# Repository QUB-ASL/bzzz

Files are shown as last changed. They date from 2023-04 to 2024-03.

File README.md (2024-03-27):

<p align="center">
bzzz-logo
</p>

<p align="center">
<em>Programmable quadcopter with ESP32 and RaspberryPi</em>
</p>

## Project Description

The autonomous systems lab at the school of EEECS of Queens University Belfast (QUB) has designed and built a quadcopter with a stabilising attitude control system and (as of v0.2.0) altitude hold. This is part of an ongoing research project whose objective is the development of control methodologies that will enable quadcopters to fly in extreme weather conditions. Currently, the quadcopter can be operated using a radio controller (RC).

## Getting started

- [Safety first](docs/SAFETY.md): read the safety guidelines
- [Contributing to this project](CONTRIBUTING.md)
- [Setting up software from scratch](docs/SETUP.md)
- [PCB design](design/README.md)
- [ESP32 documentation](include/README.md), [headers](./include) and [sources](./src)
- [Raspberry Pi code](raspberry/README.md)
- [Create a Discord bot](raspberry/DiscordBot/README.md)
- [Changelog](CHANGELOG.md)

## Design

The structure of the quadcopter is shown below

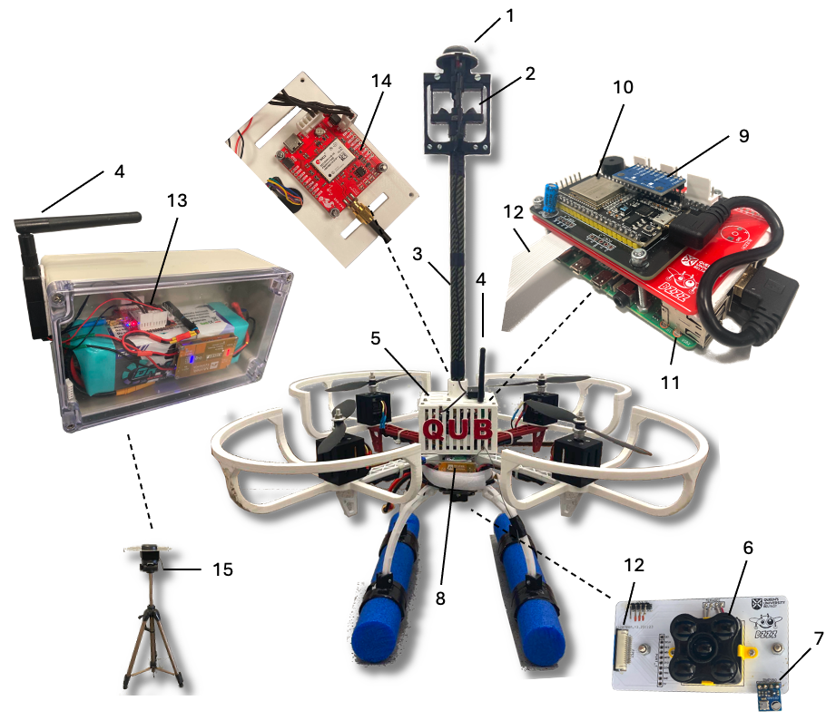
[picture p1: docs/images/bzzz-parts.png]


The parts shown in the figure are: 1. GNSS L1/L2 antenna, 2. 3D anemometer, 3. Carbon fibre pole, 4. Telemetry radio pair, 5. Box with electronics (Raspberry Pi, ESP32, IMU, GNSS module, radio receiver module), 6. Time-of-flight altimeter, 7. Barometer, 8. LiPo battery and UBEC, 9. IMU, 10. ESP32 microcontroller (attitude control system), 11. Raspberry Pi, 12. Interface between Raspberry Pi and sensors board, 13. Base station GNSS module, 14. GNSS module on the vehicle (inside the box), 15. Base GPS station.

A high-level schematic of the quadcopter with all its basic modules is shown below:

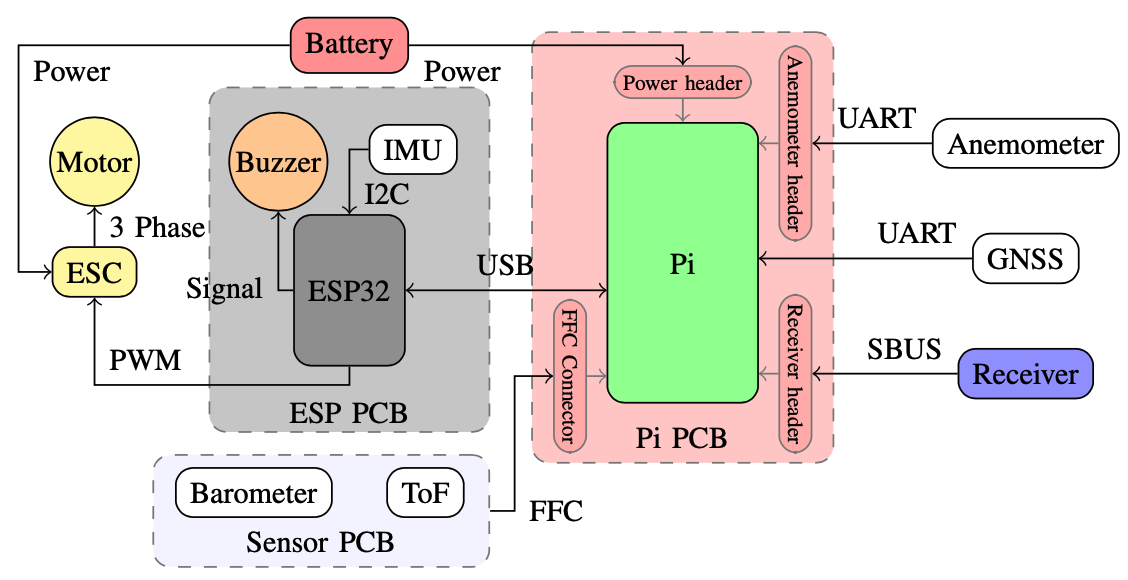
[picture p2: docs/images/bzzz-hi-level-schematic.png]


An ESP32 microcontroller is connected to an MPU9250 9-axis IMU and runs the attitude controller. 
A Raspberry Pi 4B computer is connected to a number of sensors (e.g., time-of-flight altimeter,
GPS module, and anemometer) and can run high-level tasks such as 
altitude and position control.
An RC receiver is connected to the Raspberry Pi and provides the commands of the operator.
The Raspberry Pi and the ESP32 microcontroller are connected with a USB and this allows
a bidirectional communication: the Raspberry sends tilt and throttle references to the 
ESP32 which in turn provides IMU measurements to the Raspberry Pi. 

## How to Fly 
*This is the current set up for how to fly the quadcopter*

- Make sure the quadcopter is in a safe place to fly
- Power on the battery
- Turn on the remote and wait to connect
- Arm the quadcopter by switch B
- Fly safely
- Switch D kills the quadcopter

## Videos 

<p>Testing altitude hold of bzzz:</p>

Watch the video (https://youtu.be/AMWUkB0SQi4)

<p>First flight of bzzz:</p>

Watch the video (https://youtu.be/eGNW_-LX130)

<p>Preliminary tests in the lab:</p>

Watch the video (https://youtu.be/7mFDusj9uvs)

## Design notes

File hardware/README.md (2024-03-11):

## Tests
This program performs the ESC calibrations. 

## ESC_calibration.cpp
This to to calibrate Hobbywing Skywalker ESC only. If another ESC is being used it may require recoding.

The signal to the ESC is set high before the power is provided to the ESC. 
This sets it to calibration mode.
After a particular delay the signal to the ESC is set back to low which completes the calibration. 

### Step to calibrate ESC
* Take the code from `ESC_calibration.cpp` and paste it to the `main.cpp`
* Flash it to the ESP32
* Power on the ESC
* 2 short beeps would confirm that the ESC is in calibration mode
* 3 short beeps and 1 long beep would confirm that the ESC is calibrated.

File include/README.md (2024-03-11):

# Embedded ESP32 C++ code

**About:** This software runs on the ESP32. Its job is
- To receive data from the Serial (provided by the Raspberry Pi) and parse it
- To run the attitude control algorithm
- To implement certain safety mechanisms (arming, killing, etc)

## Contents

The following files are included

| File | Description |
| --- | --- |
| `ahrs.hpp` | AHRS system (reads IMU measurements, calibrates the IMU, interfaces the Madgwick filter) |
| `config.hpp` | various constants |
| `controller.hpp`  | attitude control system |
| `fail_safe.hpp` | checks whether the serial is connected |
| `motors.hpp` | interface for the four motors |
| `quaternion.hpp`  | quaternion algebra |
| `radioEsp32Interface.hpp` | serial interface between Raspberry Pi and ESP32 |
| `util.hpp` | logging, buzzing, and other utils |

The implementations are in [`../src`](../src)

## Communication protocol

### Raspberry Pi to ESP32

The EPS32 receives over the serial the following message

```
S, yaw_rate_reference, pitch_reference_rad, roll_reference_rad, throttle_reference, trimmer_a_prcnt, trimmer_b_prcnt, trimmer_c_prcnt, trimmer_e_prcnt, encoded_switches
```

where the character "S" is used to mark the start of the message, `yaw_rate_reference` is the yaw reference rate (left stick, horizontal) in rad/sec, `pitch_reference_rad` is the pitch reference angle in rad (right stick, vertical), `roll_reference_rad` is the roll reference angle in rad (right stick, horizontal), `throttle_reference` is the throttle reference (left stick, vertical), `trimmer_a_prcnt`, `trimmer_b_prcnt` and `trimmer_c_prcnt` are the positions of the three trimmers as a number between 0 and 1, `trimmer_e_prcnt` is the position of trimmer E (right side of the RC), and lastly `encoded_switches` are the switches A, B, C, and D encoded as follows:

- bit-4 (MSB): 1-bit info of Switch B: 1 if armed else 0
- bit-3: 1-bit info of Switch A: 1 if kill_on else 0
- bits 2 and 1: 2-bit info of switch C: 00 for position DOWN, 01 for position MID, 10 for position UP
- bit-0: 1-bit info of switch D: 1 if D_on else 0

### ESP32 to Raspberry Pi

The ESP sends the following message over the serial

```
FD: q1 q2 q3 ax ay az motorFL motorFR motorBL motorBR
```

where the string "FD:" is used to mark the start of the message, `q1`, `q2`, `q3` are the vector part of the quaternion, `ax`, `ay`, `az` are the acceleration measurements from the IMU, `motorFL`, `motorFR`, `motorBL`, and `motorBR` are the PWM signals to the four motors.
 
## Headers 

This directory is intended for project header files.

A header file is a file containing C declarations and macro definitions
to be shared between several project source files. You request the use of a
header file in your project source file (C, C++, etc) located in `src` folder
by including it, with the C preprocessing directive `#include'.

```c++
// File: src/main.c

#include "header.h"

int main (void)
{
 ...
}
```

Including a header file produces the same results as copying the header file
into each source file that needs it. Such copying would be time-consuming
and error-prone. With a header file, the related declarations appear
in only one place. If they need to be changed, they can be changed in one
place, and programs that include the header file will automatically use the
new version when next recompiled. The header file eliminates the labor of
finding and changing all the copies as well as the risk that a failure to
find one copy will result in inconsistencies within a program.

In C, the usual convention is to give header files names that end with `.h'.
It is most portable to use only letters, digits, dashes, and underscores in
header file names, and at most one dot.

Read more about using header files in official GCC documentation:

* Include Syntax
* Include Operation
* Once-Only Headers
* Computed Includes

https://gcc.gnu.org/onlinedocs/cpp/Header-Files.html

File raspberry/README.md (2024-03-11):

# bzzz python package

This package contains the entire Python code to be running on Raspberry Pi. 
The following features are currently available:

1. Kalman filter estimator for altitude hold dynamics related parameter estimation.
2. Reading RC data and parsing it to ESP.
3. Altitude hold dynamics simulations.

## Installation

If you are setting up a Raspberry Pi from scratch we would recommend following the [SET_UP](docs/SET_UP.md) document.

## Dependencies
There are a few packages that can not be installed in the virtual environment by `pip` therfore should be instaled system wide.

To do this run
```
sudo apt-get install libopenblas-dev libatlas-base-dev
```

## virtual environment
Next a virtual environment can be created by (we have tested this with Python 3.11.2):
```
python -m venv venv_bzzz
```
For older versions of python use:
```
virtualenv -p python3 venv_bzzz
```

Then, activate the virtual environment
```
source  venv_bzzz/bin/activate
```

and install the requaried packages.
```
cd bzzz/raspberry
pip install .
```

Now the `main.py` script can be ran by:
```
sudo pigpiod
python main.py
```

## How to run the main Raspberry Pi code on start-up
After the virtual environment and dependencies have been installed as described above, a script can be used to atuomatically run the main Raspberry
Pi code on start-up.

To do this, the `run_main_on_start_up.sh` can be added to the users crontab by:

```
crontab -e
```
Then add the following:

```
@reboot sleep 10 && ~/bzzz/raspberry/run_main_on_start_up.sh
```

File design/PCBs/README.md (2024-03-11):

# How to open

1. For quickly viewing the schematic or PCB's, please use the provided `*.png` files. 
2. To open schematic and PCB sources, install and use [EasyEDA](https://easyeda.com/page/download).
3. To view the provided Gerber files, you can use any preferred software. An easy to use software is [Gerbv](https://gerbv.github.io/).

# Schematics & Board layouts

The following images are to scale, to see larger images see `*_x2.5.png` files. 

## ESP board with 2 IMU's

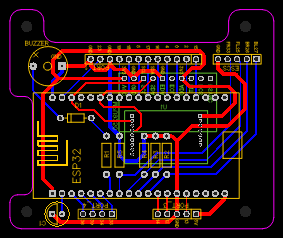
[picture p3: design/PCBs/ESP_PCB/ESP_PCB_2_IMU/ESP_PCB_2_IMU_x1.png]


## ESP schematic 2 IMU's

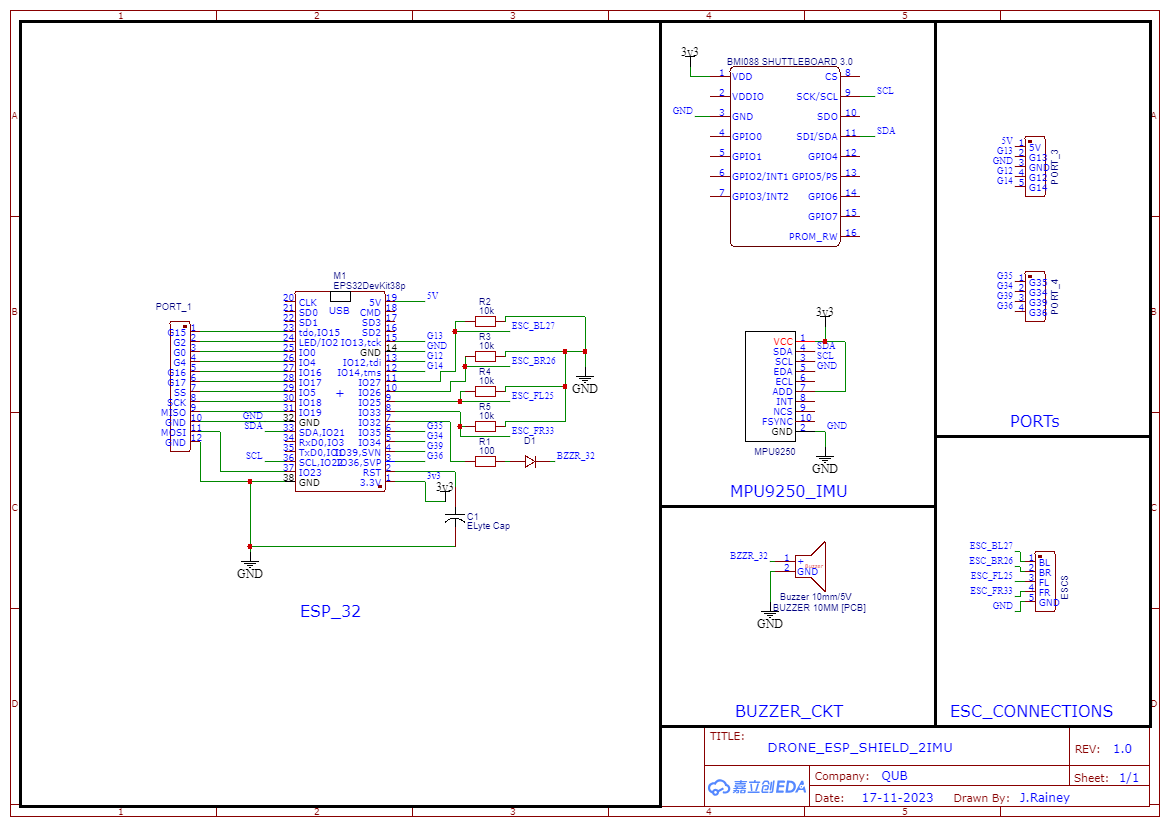
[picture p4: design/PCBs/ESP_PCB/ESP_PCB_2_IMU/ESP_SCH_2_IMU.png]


## Pi board with FPC/FFC

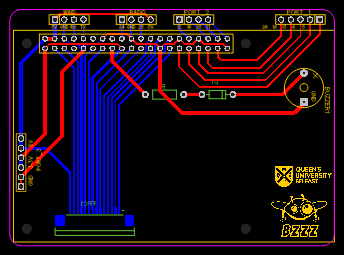
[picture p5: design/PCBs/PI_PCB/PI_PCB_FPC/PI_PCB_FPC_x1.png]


## Pi schematic with FPC/FFC

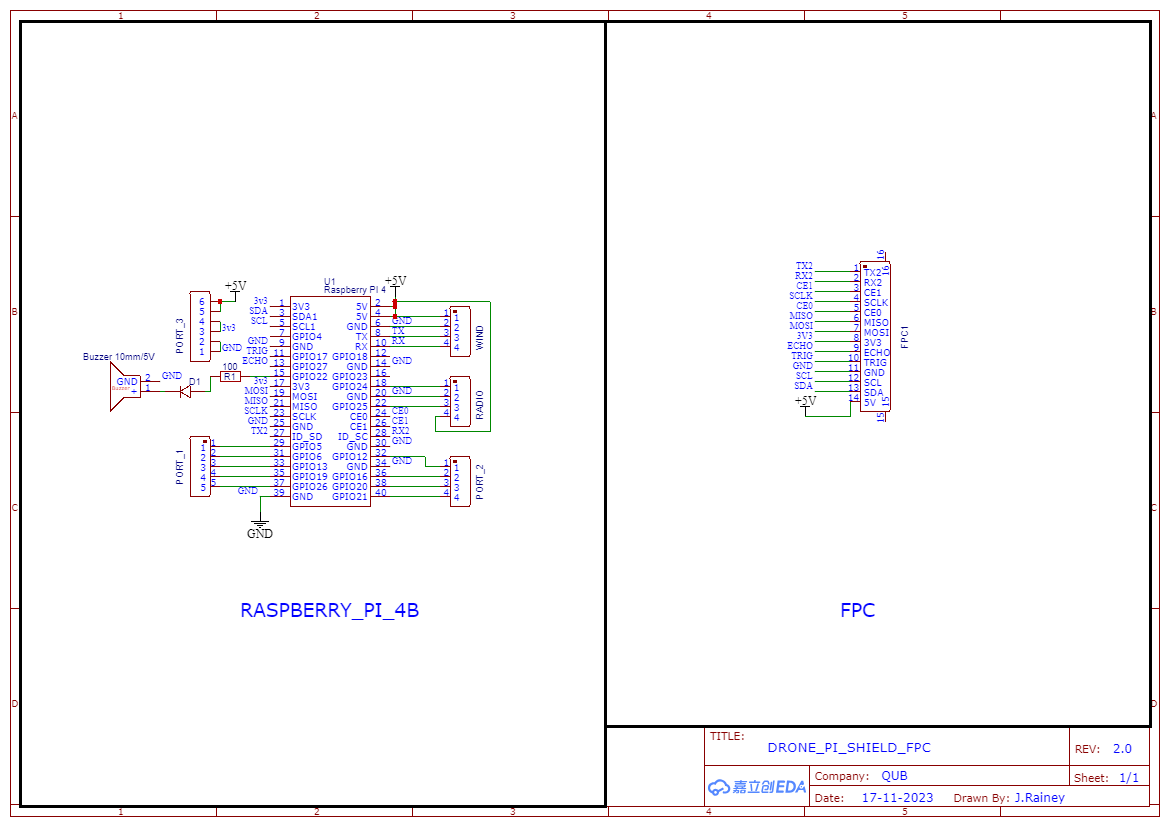
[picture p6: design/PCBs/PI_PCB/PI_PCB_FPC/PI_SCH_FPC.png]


## Sensor Board with FPC/FFC

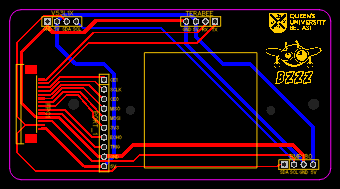
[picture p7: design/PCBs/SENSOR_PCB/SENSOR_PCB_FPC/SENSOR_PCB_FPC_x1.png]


### Sensor schematic with FPC/FFC

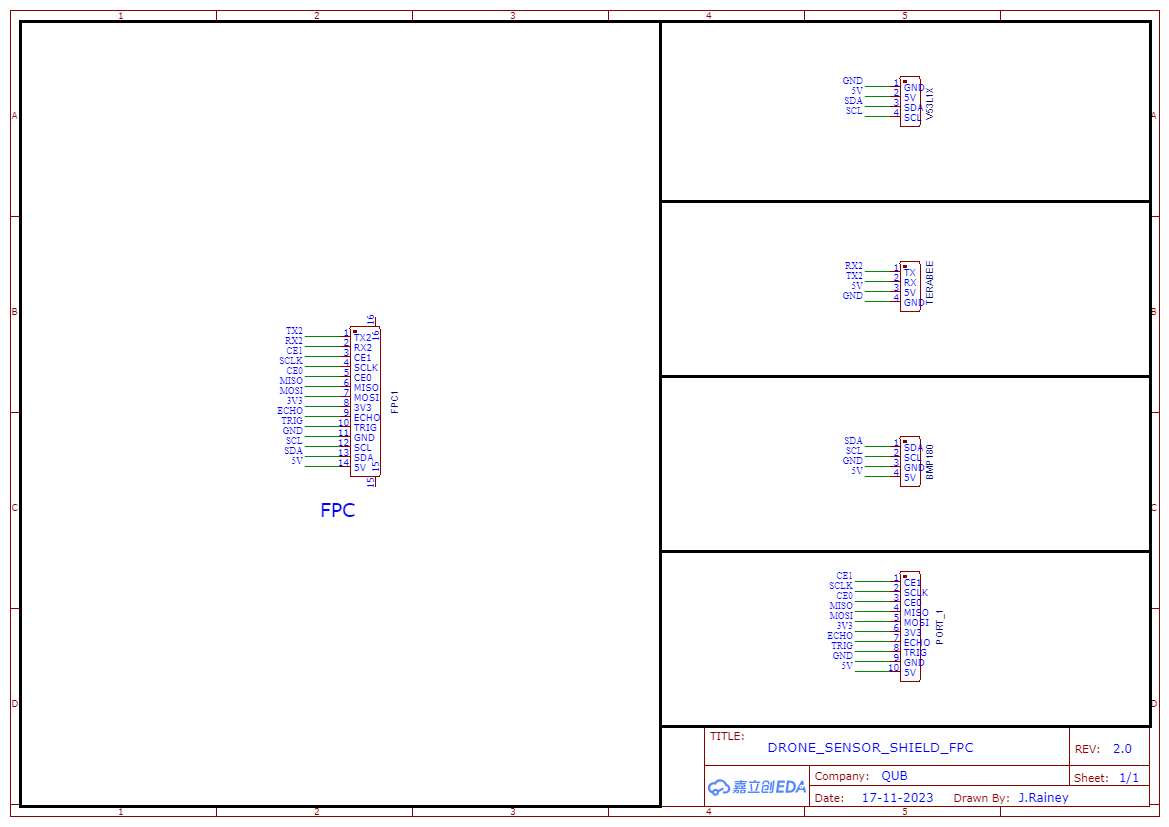
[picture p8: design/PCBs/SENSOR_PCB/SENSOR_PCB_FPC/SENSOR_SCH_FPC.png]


# BOM

## Genral Parts

* [Molex KK Crimp Terminal Contact](https://uk.rs-online.com/web/p/crimp-contacts/0467598)
* [PCB Socket long leg 20 x1](https://uk.rs-online.com/web/p/pcb-sockets/2081703)
* [PCB Socket short leg 32 x1](https://uk.rs-online.com/web/p/pcb-sockets/2081707)
* [14 way FFC Ribbon Cable](https://uk.rs-online.com/web/p/ribbon-cable/7635694?gb=s)

## ESP board

* [ESP32](https://www.amazon.co.uk/dp/B0BYMWQT37?_encoding=UTF8&ref_=cm_sw_r_cp_ud_dp_3BHTPX8BNFBTKMHN5VE3&th=1)
* [MPU9250 IMU](https://hobbycomponents.com/sensors/720-mpu9250-9-axis-9dof-acc-gyro-compass-module)
* [BMI088 IMU](https://uk.rs-online.com/web/p/sensor-development-tools/2457082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)
* [BNO055](https://thepihut.com/products/adafruit-9-dof-absolute-orientation-imu-fusion-breakout-bno055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)
* [Molex KK Pin Header, 4 X 1](https://uk.rs-online.com/web/p/pcb-headers/4838483)
* [Molex KK Connector Housing 4 x 1](https://uk.rs-online.com/web/p/wire-housings-plugs/6795388)
* [Molex KK Pin Header, 5 X 1](https://uk.rs-online.com/web/p/pcb-headers/4838499)
* [Molex KK Connector Housing 5 x 1](https://uk.rs-online.com/web/p/wire-housings-plugs/6795385)
  
## Pi board

* [Raspberry Pi](https://thepihut.com/products/raspberry-pi-4-model-b?variant=31994565689406)
* [Pi GPIO Header](https://thepihut.com/products/gpio-stacking-header-for-pi-a-b-pi-2-pi-3)
* [Molex KK Pin Header, 4 X 1](https://uk.rs-online.com/web/p/pcb-headers/4838483)
* [Molex KK Connector Housing 4 x 1](https://uk.rs-online.com/web/p/wire-housings-plugs/6795388)
* [Molex KK Pin Header, 5 X 1](https://uk.rs-online.com/web/p/pcb-headers/4838499)
* [Molex KK Connector Housing 5 x 1](https://uk.rs-online.com/web/p/wire-housings-plugs/6795385)
* [Molex KK Pin Header, 6 X 1](https://uk.rs-online.com/web/p/pcb-headers/6795593)
* [Molex KK Connector Housing 6 x 1](https://uk.rs-online.com/web/p/wire-housings-plugs/6795391)
* [14 way FFC Connector](https://uk.rs-online.com/web/p/fpc-connectors/7632578)

## Sensor board

* [Teraranger Evo](https://www.terabee.com/sensors-modules/lidar-tof-range-finders/#individual-distance-measurement-sensors)
* [VL53L0X Time of Flight sensor](https://uk.rs-online.com/web/p/sensor-development-tools/1845087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)
* [BMP180](https://www.amazon.co.uk/AZDelivery-BMP180-Barometric-Pressure-Sensor/dp/B07D8S617X?th=1)
* [Molex KK Pin Header, 4 X 1](https://uk.rs-online.com/web/p/pcb-headers/4838483)
* [Molex KK Connector Housing 4 x 1](https://uk.rs-online.com/web/p/wire-housings-plugs/6795388)
* [14 way FFC Connector](https://uk.rs-online.com/web/p/fpc-connectors/7632578)

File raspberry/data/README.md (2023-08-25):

# Data files

CSV files with the following columns:

- `timestamp_ms` timestamp in milliseconds
- `throttle_ref` throttle reference from the RC
- `yaw` yaw angle in rad
- `pitch` pitch angle in rad
- `roll` roll angle in rad
- `tof_measurement` measurement from the ToF sensor in mm
- `accX` acc_x from the accelerometer, in m/s^2
- `accY` acc_y from the accelerometer, in m/s^2 
- `accZ` acc_z from the accelerometer, in m/s^2
- `altitude_ref` altitude reference in m
- `RC data` dump of the RC data as a string - exactly as encoded by the RC parser 
- `mot_FL` PWM signal to the forward left motor (int)
- `mot_FR` PWM signal to the forward right motor (int)
- `mot_BL` PWM signal to the backward left motor (int)
- `mot_BR` PWM signal to the backward right motor (int)
- `KF_altitutde_est` altitude estimate from KF in m
- `KF_velocity_z_est` velocity estimate from KF in m/s
- `KF_alpha_est` KF estimate of alpha
- `KF_beta_est` KF estimate of beta

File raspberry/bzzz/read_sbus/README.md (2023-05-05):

# read_sbus
[`read_sbus`](https://github.com/VermontCoder/read_sbus) is a module for the Rasperry Pi to read SBus protocol input. SBus is a protocol used by many RC receivers to send data to flight controllers to control RC aircraft,
quadcopters or cars. SBus has an advantage over standard PWM in that up to 16 channels of data can be sent over a single data line.

## Software Requirements
`read_sbus` makes use of two libraries.

- the [pigpio](https://abyz.me.uk/rpi/pigpio/) library. That can be installed as follows

```
sudo apt-get update
sudo apt-get install pigpio
```

- the [bitarray](https://pypi.org/project/bitarray/) library. 

Then, create a virtual environment as follows

```
virtualenv -p python3 venv
source venv/bin/activate
```

and install the following Python packages

```
pip install bitarray pigpio pyserial
```

## Raspberry Pi with ESP32

The raspberry Pi will be used for any high level control, while the ESP32 is used for the low level control (attitude control). 
Currently the Pi is used to receive the radio data and send it to the ESP32. In order to do this the file [`read_sbus_from_GPIO_receiver.py`](https://github.com/QUB-ASL/bzzz/blob/feature/raspberry-readsbus/raspberry/read_sbus/read_sbus_from_GPIO_receiver.py) was created. The radio data is sent from the Pi to the ESP32 via serial.

To receive data from the radio remote control and send it to the ESP32 open a terminal on Raspberry Pi and execute the following 
```
sudo pigpiod
python bzzz/raspberry/read_sbus/read_sbus_from_GPIO_receiver.py
```

## Hardware Test

In order to check that the receiver is connected to the Pi correctly and the remote control and reciever are bound properly, the file [`hw_test_receiver.py`](https://github.com/QUB-ASL/bzzz/blob/feature/raspberry-readsbus/hardware/tests/hw_test_receiver.py) was created. The data that is received from the reciever will be printed.

To test the Pi is receiving the correct data open a terminal on Raspberry Pi and execute the following 
```
sudo pigpiod
python hw_test_receiver.py
```

## Reference 
For more information on the `read_sbus` module visit https://github.com/VermontCoder/read_sbus

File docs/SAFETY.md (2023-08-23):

# General lab rules

Last updated: 24 August 2023

**Table of Contents**

1. [Key hazards](#1-key-hazards)
2. [The basics](#2-the-basics)
3. [Soldering](#3-soldering)
4. [Quadcopter motors](#4-quadcopter-motors)
5. [LiPo batteries](#5-lipo-batteries)
6. [Test flights](#6-test-flights)
7. [Fire safety](#7-fire-safety)
8. [Emergency numbers](#8-emergency-numbers)
9. [First aid](#9-first-aid-kit)
10. [Endnotes](#9-endnotes)

## 1. Key hazards

In the quadcopter lab (part of the autonomous systems lab) everyone should be aware of the following types of hazards:

- **Mechanical** (e.g., electric motors of quadcopters)
- **Thermal** (e.g., while soldering or glue guns)
- **Hazardous smokes** (e.g., from soldering)
- **Electrical** (low risk, as we typically work with low-voltage equipment)
- **Fire or explosions** e.g., from mishandling LiPo batteries

Our goal is to *identify* any possible hazards and *minimise* the likelihood of such hazards.

This document attempts to identify any possible risks and propose safety measures; it *complements* the [health and safety regulations and guidance](https://www.qub.ac.uk/directorates/EstatesDirectorate/UniversitySafetyService/HealthandSafetyPoliciesandGuidance/) of the university.

## 2. The basics

- Health and safety is everyone's responsibility
- If you suspect that you have identified a hazard, you should contact your line manager
- Any accidents must be reported to your line manager

> Important: In the case of an **emergency** where there is an imminent and serious danger to people or property, then the appropriate emergency services should be called. To do this from a University telephone, dial **2222** to contact the University Control Room operator or 9-999 to contact Police, Fire, and Ambulance services.

## 3. Soldering 

Some common risks associated with soldering include exposure to hazardous chemicals, eye injuries, burns, and inhalation of fumes and smoke. When soldering, the solder and flux emit fumes that can cause respiratory issues if inhaled in high quantities. Additionally, the soldering iron can become extremely hot (around 400C) and cause burns to the skin or eyes if safety controls are not in place. 

As a result:

- Do not attempt to use the soldering iron unless you have been trained; contact your line manager first.
- Never touch the element of the soldering iron.
- Use tweezers where possible and avoid touching the wires you are soldering with your hands.
- Keep the cleaning sponge wet during use.
- Always return the soldering iron to its stand when not in use. Never put it down on the workbench.
- Turn unit off and unplug when not in use.
- Wear eye protection as the solder can "spit" in any direction.
- Use rosin-free and lead-free solders wherever possible.
- Always wash your hands with soap and water after soldering.

You may find more information at the [webpage](https://safety.eng.cam.ac.uk/safe-working/copy_of_soldering-safety) of the Dept of Engineering Health and Safety of the University of Cambridge.

## 4. Quadcopter motors

The brushless motors used on a quadcopter can spin up to several thousands RPM, therefore, if you are close to a spinning motor you risk getting injured. 

At all times, observe the following safety instructions:

- Never touch a spinning motor with your hands or with a tool or through a piece of clothing
- When you are close to a spinning motor you must not wear a lanyard, tie, scarfs. If you are wearing a hoodie with drawstrings, put them inside so that they do not hang. Any hanging string is likely to be caught up by a motor leading to injury.
- Wear protective glasses: even when you are operating a motor without the propellers attached, there is a chance that a bolt becomes loose and flies off at a high speed.
- Periodically (at least twice a day), make sure that the little grub screws at the bottom part of the motors are not loose. Of course, you should not tighten them too much.
- At least once a day and every time before performing test flights, you should check to make sure that the bolts that hold the motors on the horizontal metallic rods are tightly screwed.

> :warning: **KEEP IN MIND**
> - When the ESCs are **armed**, the motors can start to rotate at any time.
> - In case it is not possible to kill the quadcopter (e.g., due to a fault), wear protective equipment (glasses and proper gloves) before approaching.
> - After you flip the ARM switch (switch B on the RC) treat the motors as if they are armed - even if the ESCs are beeping, the motors may be armed.

## 5. LiPo batteries

### 5.1. Hazards 

There are several hazards associated with LiPo batteries, such as:

- **Fire and explosion**: Mishandling of LiPo batteries can lead to fire, explosions, and toxic smoke inhalation. This is because LiPo batteries contain highly volatile and flammable electrolytes that can catch fire if they are damaged, overcharged, or punctured.
- **Thermal runaway**: LiPo batteries can undergo a process called thermal runaway, where a small thermal event or overcharging can cause the battery to rapidly heat up, leading to a chain reaction and causing the battery to vent, catch fire, or explode.
- **Physical damage**: LiPo batteries are sensitive to physical damage, such as punctures or crushing, which can cause them to catch fire or explode.
- **Voltage deviation**: If the voltages across the cells deviate too much from each other (5 ~ 10mV), the battery can become unstable and dangerous.

Therefore, it is important to handle LiPo batteries with care.



### 5.2. How to charge and store a LiPo battery

- LiPo batteries should not be stored fully charged. Instead, they should be brought down to **storage charge**, which corresponds to about 3.8V per cell. A LiPo battery not at storage voltage will degrade and the effect is cumulative: keeping a battery fully charged for 10 consecutive days is the same as keeping it fully charged for 1 day on 10 different days. 

> It is highly recommended that we storage-charge the LiPo batteries at the end of every day.

- It is recommended to use a **LiPo battery bag** when charging a LiPo battery to provide an extra layer of protection against fire and explosion.
- Never let a battery voltage fall below critical level. If the voltage in a cell falls below 3.2V it can be permanently damaged. 
- Never overcharge a battery. If the voltage of a cell exceeds 4.2V it can burst into flames. 
- Never short-circuit a battery.
- Follow proper disposing guidelines before discarding a battery.
- Any bulge, smoke from a battery must be dealt with serious caution.

> Read more about LiPo batteries [here](https://fpvfc.org/beginners-guide-to-lipo-batteries).

## 6. Test flights

> **Read first:** [Quadcopter motors](#4-quadcopter-motors)

When attaching the propellers, observe the following safety instructions:

- Attach the propellers carefully and tightly. 
- In case a propeller seems to vibrate excessively, disarm the motors, disconnect the battery, and (i) check the propellers for structural damage, (ii) make sure all screws are tightly screwed.
- Never use carbon fibre propellers as they can cause deep lacerations in case of an accident; use standard nylon propellers instead.

### 6.1. Before a test flight

1. Put on your protective glasses
2. Bring the quadcopter inside the netted area
3. After you power the quadcopter walk outside the net
4. If you need to use the test bench, make sure that (i) the ball joint is securely screwed on the base of the quadcopter, (ii) the base of the ball joint is not loose (check this before every flight)
5. Everyone must be alert.
6. Have the kill switch at the ready and be alert.
7. Make sure there are no gaps in the netting.

### 6.2. During a test flight

1. Do not enter the netting area.
2. Do not leave the drone unattended.
3. Be alert.
5. Do not go near the spinning propellers.
6. If any propeller or part of the drone comes loose, disarm immediately and disconnect the battery.

### 6.3. At the end of a test flight

1. Make sure you have disarmed using the kill switch on the RC.
2. Disconnect the battery.
3. Recharge the battery if necessary.

## 7. Fire safety

Firstly, familiarise with the [Fire Safety guidelines](https://www.qub.ac.uk/directorates/EstatesDirectorate/Services/FireSafety/) of the university.

In our lab a fire can be caused by any of the following reasons:

- Mishandling LiPo batteries
- Misusing the soldering iron or a glue gun
- Faulty electric circuits or misusing electric circuits (e.g., causing a short circuit)

To minimise the risk of fire we must always follow the [fire safety guidelines](https://www.qub.ac.uk/directorates/EstatesDirectorate/Services/FireSafety/) of the university. 

### 7.1. A few things about fire safety

- The main cause of fire is **people**
- The lab and the building is equipped with **fire doors** that can help to prevent the spread of smoke for at least 30 minutes to allow a safe exit in case of a fire. They are fitted with closing devices to ensure that the doors are in the correct position. Note that wedging fire doors open is illegal, against the university policy and unsafe. There are safe ways to hold them open if necessary.
- Do not use fire fighting equipment unless you have received training. Keep in mind that CO<sub>2</sub> fire extinguishers should be used on live electrical fires.
- Familiarise with the safety signage and notices in the building.

### 7.2. In case of a fire

If you discover a fire or even **suspect** a fire (through sight or smell), then **raise the alarm** by pressing the nearest available fire alarm manual call point.

The procedure is:

- Close the door
- Sound the fire alarm
- Ensure that Security have been informed
- Assist in the evacuation
- Tackle the fire if you are trained and someone is with you
- Immediately leave the building by the nearest available fire exit
- Do not use the elevators
- Do not stop to collect your personal belongings
- Report to the designated fire assembly point
- Do not re-enter the building until you are told it is safe to do so

## 8. Emergency numbers

- QUB security on extension 2222
- Off campus: dial 999 and ask for the fire and rescue service

## 9. First aid kit

A first aid kit is available in the lab. Make sure you know where it is and familiarise yourself with its contents, which are:

- A first aid guidance leaflet (read it carefully!)
- 20 HypaPlast washproof plasters
- 2 HypaCover eye dressings
- 2 HypaBand triangular bandages
- 12 HypaBand safety pins
- 6 HypaCover first aid dressings (12x12cm)
- 2 HypaCover first aid dressings (18x18cm)
- 6 HypaClean sterile wipes
- 3 pairs of HypaTouch disposable gloves
- 2 HypaClens eye wash bottles (500ml)

## 10. Endnotes

- No equipment leaves the lab
- Before you leave the lab:
  - switch off any electronics/electrical equipment (esp. battery chargers and soldering irons)
  - turn off the lights
  - lock the door

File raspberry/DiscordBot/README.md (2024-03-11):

## QUB ASL Discord bots

### How to create a new bot and get a token

[This video](https://discord.is-serious.business/6fd481.mp4) explains how to create a bot and obtain a token. 

You need to:

1. Visit https://discord.com/developers/applications/
2. Select "New application" (top right corner)
3. Give your bot a name. Our naming convention in bzzz is that all bots have a name that starts with `BOT_`. For example `BOT_Pi_1`. Choose a unique name for your bot.
4. In the left sidebar, go to "bot" and make sure that all options under "Privileged Gateway Intents" are active.  Don't touch anything else.

To get the token of your bot select "Reset Token". Then the token will be reset and revealed. Copy the token and paste it into a file named `token.private` in this folder (you need to create the file). Each agent (each Raspberry Pi) will have a unique token.

The next step is to invite your bot to the server.

### Invite the bot

To invite your bot, follow these steps

1. Ask @alphaville, @jamie-54 or any other member for an invitation to the Discord server and accept it. Ask @alphaville for admin privileges 
2. Visit https://discord.com/developers/applications
3. Select your bot
4. Go to "OAuth2" and then "URL Generator"
5. From the list of scopes, select "bot"
6. From the list below select "Manage Roles", "Manage Channels", "Read messages/view channels", "Send messages", "Manage messages", "Embed links", "Attach files", "Read message history", "Use slash commands", "Connect" and "Speak"
7. Copy the link from below
8. Follow the link to invite your bot to the server

### How to run the client

To run the client, first you need to create a virtual environment with Python 3 (we have tested this with Python 3.11.2):

```
python -m venv venv_bot
```

For older versions of Python a virtual environment can be created by (we have tested this with Python 3.9):

```
virtualenv -p python3 venv_bot
```

Then, activate the virtual environment

```
source  venv_bot/bin/activate
```

and install the following packages

```
pip install discord.py
pip install netifaces
```

Then, just run the script

```
cd bzzz/raspberry/DiscordBot
python main.py
```

### How to run the client on Start_up

After the virtual environment and dependencies have been installed as described above, a script can be used to automatically run the client on start_up.

To do this, the `run_DiscordBot_on_start_up.sh` can be added to the user's crontab by:

```
crontab -e
```
Then add the following:

```
@reboot sleep 10 && ~/bzzz/raspberry/DiscordBot/run_DiscordBot_on_start_up.sh
```

### Chatting with the bot

Firstly, you need to join our private Discord server. Ask one of the team members for an invitation.

In the list of participants you can see which agents (bots) are live. Type `.ip`[^1] to get their IPs. To format the output using markdown, use `.ip p` (here 'p' stands for 'pretty')

[^1]: It is not case-sensitive, so `.IP` works as well

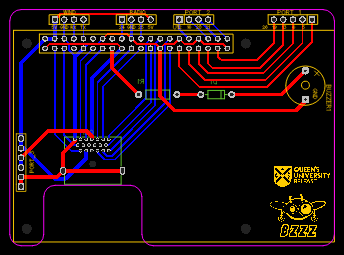
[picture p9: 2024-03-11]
design/PCBs/PI_PCB/PI_PCB_HDMI/PI_PCB_HDMI_x1.png

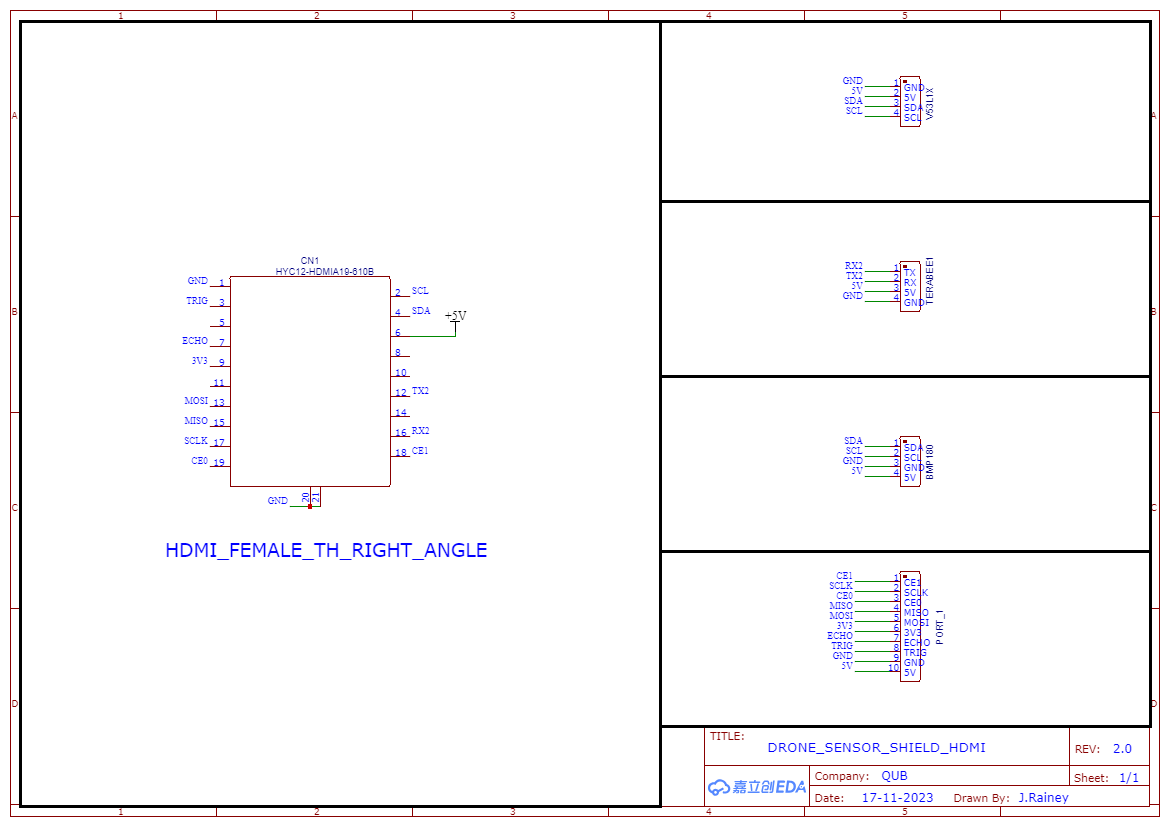
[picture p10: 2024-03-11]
design/PCBs/SENSOR_PCB/SENSOR_PCB_HDMI/SENSOR_SCH_HDMI.png

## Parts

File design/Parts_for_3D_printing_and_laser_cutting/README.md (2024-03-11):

# Parts for 3D printing
The above folders include editable Autodesk Fusion 360 files (.f3d) and STL files that can be 3D printed.

## Anemometer case
This case is to protect the Trisonica Mini ultrasonic wind anemometer that will be attached to the quadcopter.
It also has a stand for attaching the GNSS Antenna. 

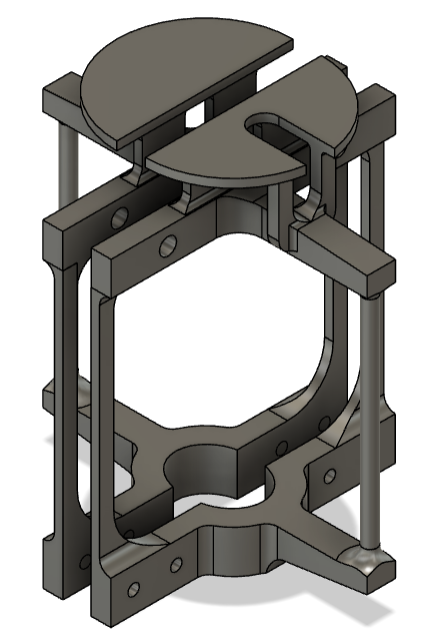
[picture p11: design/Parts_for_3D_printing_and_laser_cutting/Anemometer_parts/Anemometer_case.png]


## The following parts are designed for the F450 quadcopter frame

## Controller case
The controller case seen below, is used to house and protect the Raspberry Pi, ESP32 and the associated PCB's and electronics. It is designed to replace the 
F450 quadcopter frames top plate, has holes and slots in the correct place for wires to pass through and has our logo and the universites initials on it.

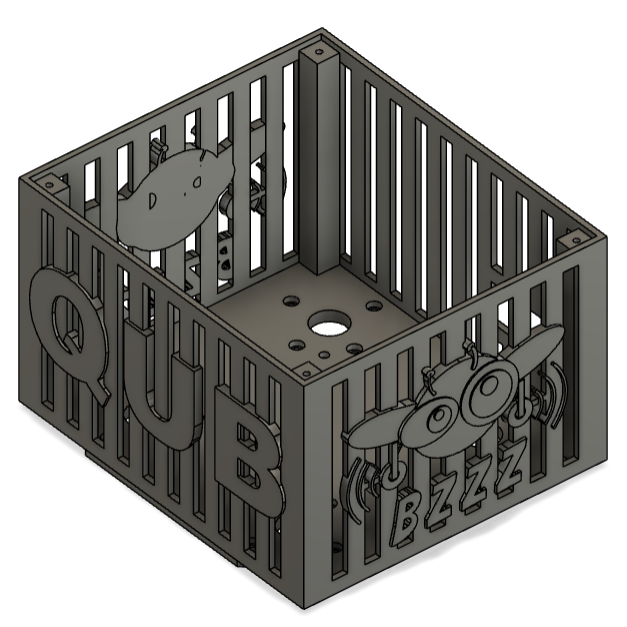
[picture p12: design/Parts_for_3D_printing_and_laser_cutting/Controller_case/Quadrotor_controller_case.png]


The controller case lid fits the case above and has a flange that a 22mm pipe can fit in. This is used to attach the anemometer above the quadcopter.
The lid also has holes to attach the appropriate GPS/GNSS modules to the inside of the lid. The photo below shows the controller case lid.

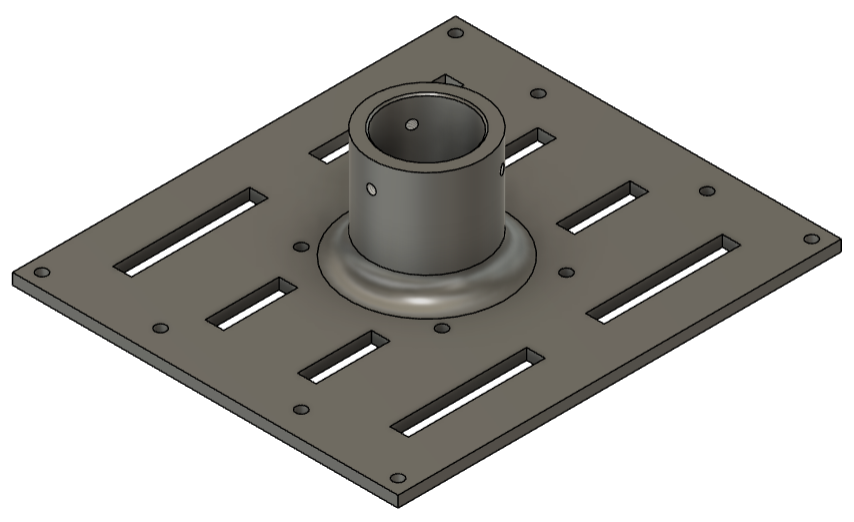
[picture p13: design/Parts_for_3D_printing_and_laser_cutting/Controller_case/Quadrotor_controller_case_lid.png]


## Motor stands
The 'Non-rotating' motor stand as seen in the photo below is for directly mounting a outrunner motor such as the 
'PROPDRIVE v2 3536' or 'Turnigy Air 3730' to the F450 quadcopter frame.

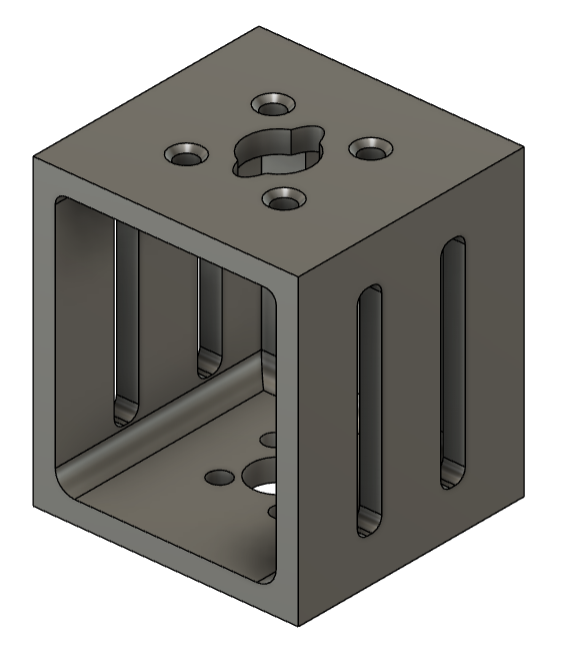
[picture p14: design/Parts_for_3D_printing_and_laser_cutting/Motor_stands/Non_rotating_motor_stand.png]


The 'Rotating' motor stand as seen in the photo below is for attaching a rod between two rotating motor stands and mounting the outrunner motors 
to the rod to add an extra degree of fredom to help control the quadcopter. A hole is included in the top so a screw can be put through the rod to 
stop it rotating if needed. The offset hole is for a rod where there holes were not drilled straight.

This set up can be seen in [Altitude Hold Video](https://youtu.be/AMWUkB0SQi4) 

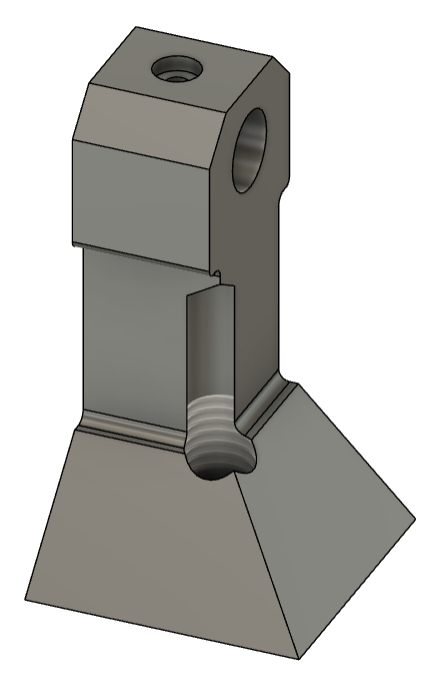
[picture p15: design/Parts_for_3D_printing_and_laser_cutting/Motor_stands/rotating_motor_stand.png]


## Propeller guards
Depending on which motor stand is used a different propeller guard will be needed.

If the 'Non-rotating' motor stand is used the 'Symmetrical' propeller guard as seen in the photo below can be used.

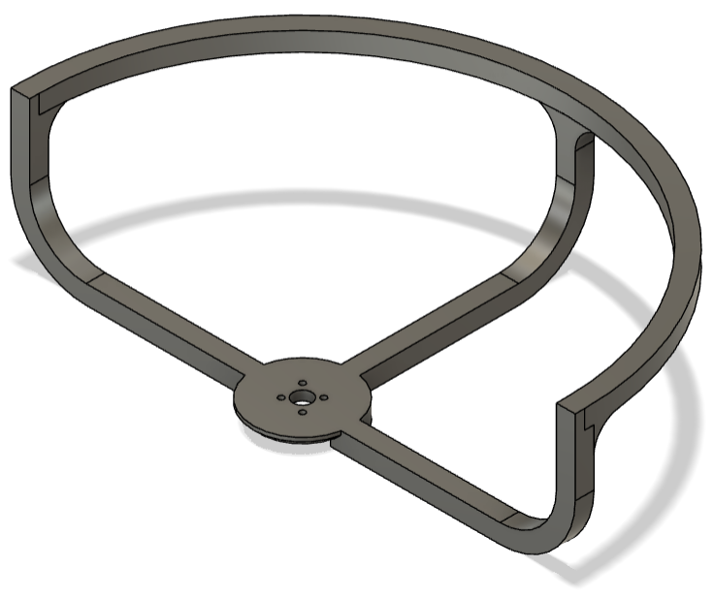
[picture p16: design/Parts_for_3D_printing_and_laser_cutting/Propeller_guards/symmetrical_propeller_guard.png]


If the 'Rotating' motor stand is used the 'Offset' propeller guard as seen below is used as the motor is no longer directly in centre of the frame.

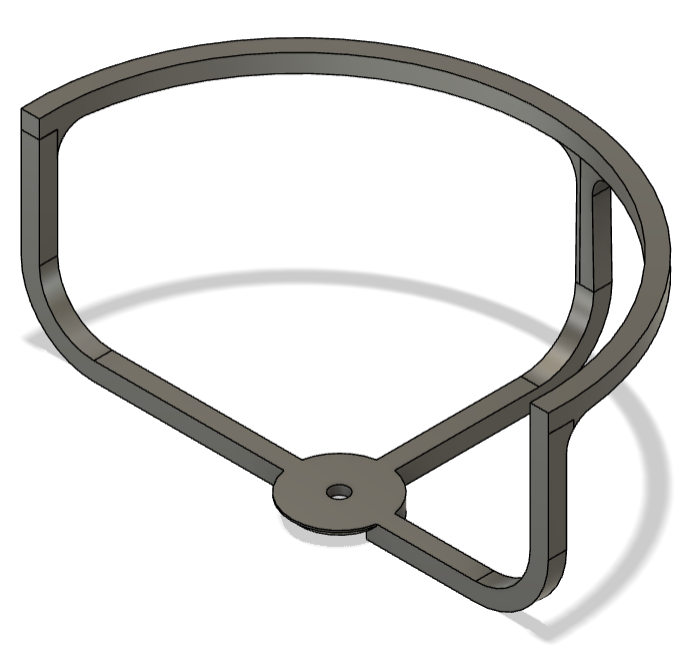
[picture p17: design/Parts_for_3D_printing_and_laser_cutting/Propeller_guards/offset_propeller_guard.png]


## Frame base support 
This is used to help support the power disturbution board on the base of the quadcopter frame.

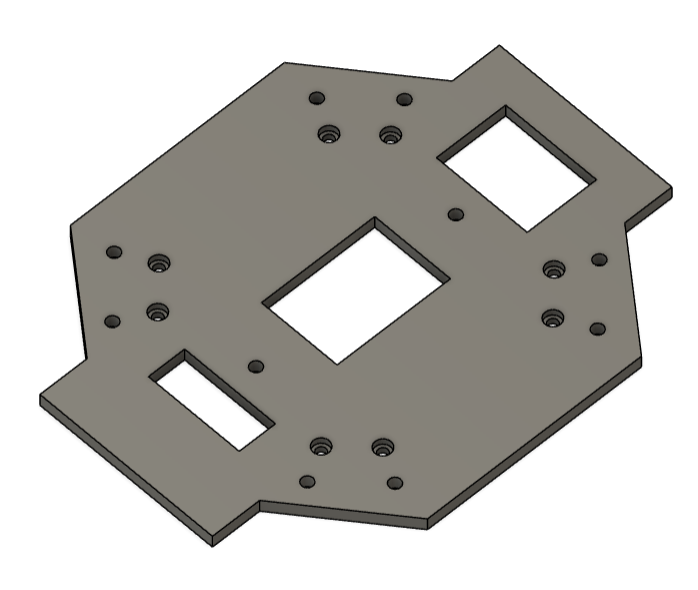
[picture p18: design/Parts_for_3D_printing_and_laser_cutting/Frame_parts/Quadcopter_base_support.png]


## GNSS and Antenna Parts 

## Base station adapter

The base station adapter is used to attach the base station antenna to a tripod and can be seen in the Photo bellow.



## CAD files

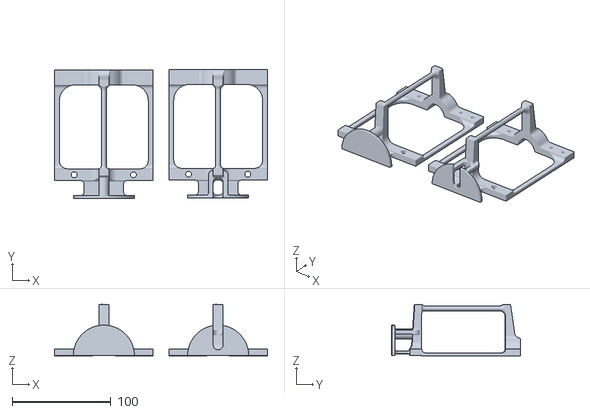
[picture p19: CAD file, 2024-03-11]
design/Parts_for_3D_printing_and_laser_cutting/Anemometer_parts/Amemometer_case v6.stl
215.8 x 130.5 x 52.3

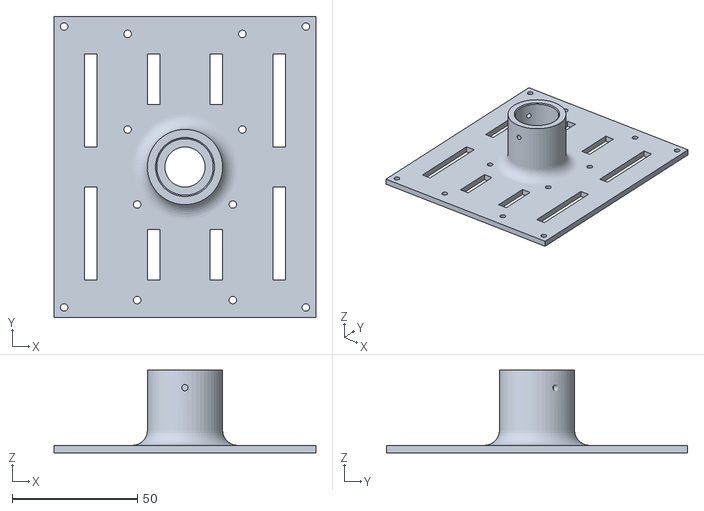
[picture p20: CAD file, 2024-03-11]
design/Parts_for_3D_printing_and_laser_cutting/Controller_case/Quadrotor_controller_case_lid v7.stl
104.4 x 120.0 x 33.0

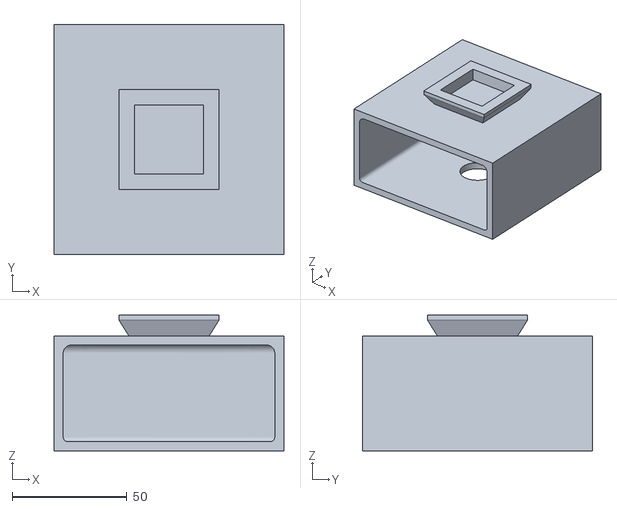
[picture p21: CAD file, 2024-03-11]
design/Parts_for_3D_printing_and_laser_cutting/GPS_and_antenna_parts/Base_station_adapter v7.stl
100.0 x 100.0 x 59.0

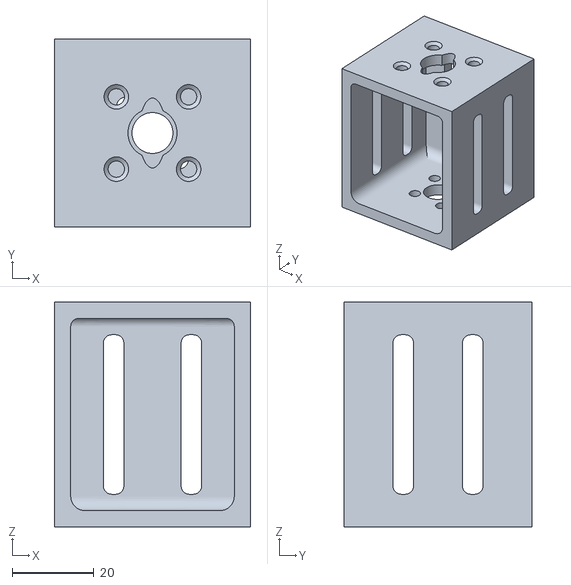
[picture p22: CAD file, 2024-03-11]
design/Parts_for_3D_printing_and_laser_cutting/Motor_stands/non_rotating_motor_stand v12.stl
48.0 x 46.0 x 55.0

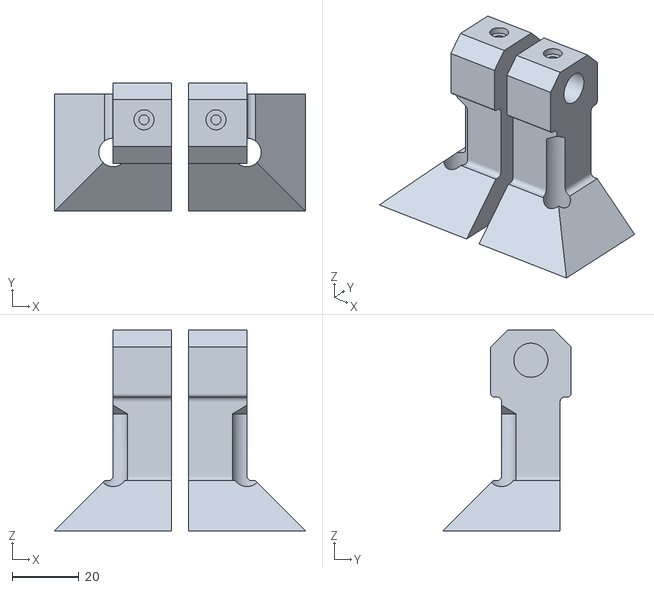
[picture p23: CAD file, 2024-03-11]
design/Parts_for_3D_printing_and_laser_cutting/Motor_stands/rotating_motor_stand_offset_hole_set v1.stl
75.0 x 38.2 x 60.0

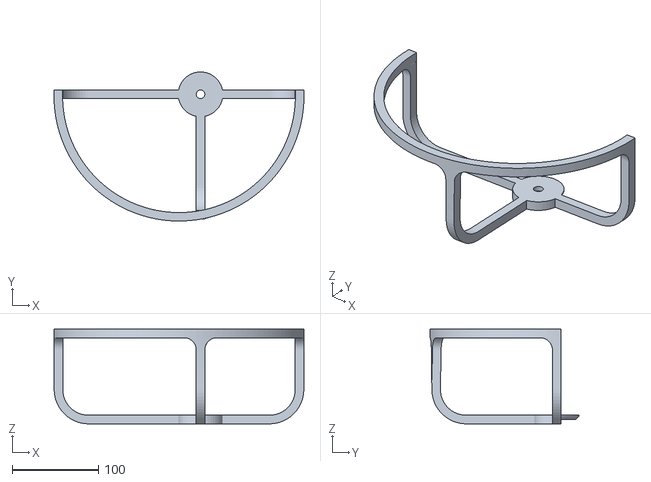
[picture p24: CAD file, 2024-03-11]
design/Parts_for_3D_printing_and_laser_cutting/Propeller_guards/offset_propeller_guard_mirrored v1.stl
290.3 x 173.1 x 110.0

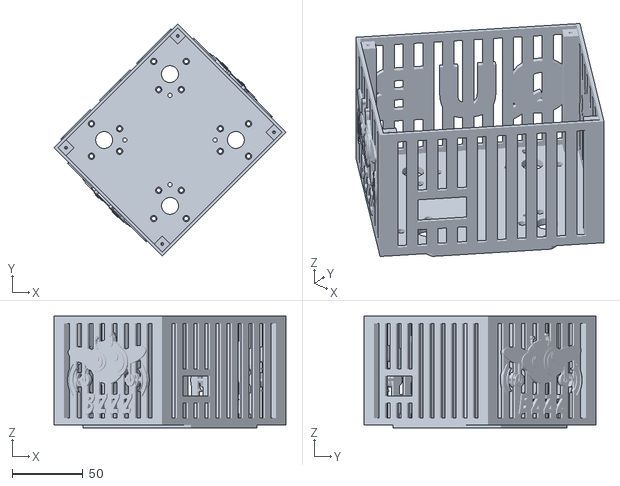
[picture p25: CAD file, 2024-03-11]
design/Parts_for_3D_printing_and_laser_cutting/Controller_case/Quadrotor_controller_case v6.stl
164.4 x 164.4 x 79.0

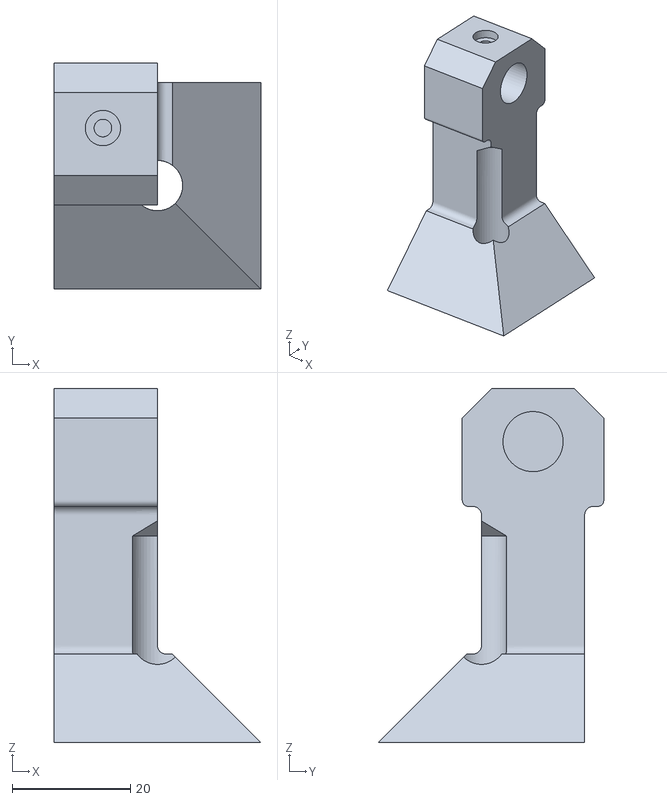
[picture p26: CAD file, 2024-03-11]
design/Parts_for_3D_printing_and_laser_cutting/Motor_stands/rotating_motor_stand_offset_hole v1.stl
35.0 x 38.2 x 60.0

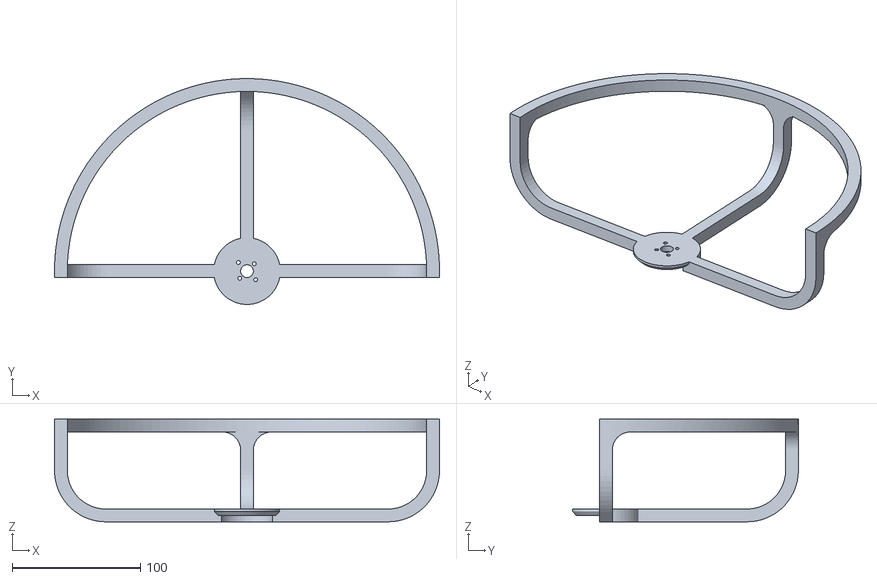
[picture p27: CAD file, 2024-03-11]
design/Parts_for_3D_printing_and_laser_cutting/Propeller_guards/symmetrical_propeller_guard v3.stl
300.0 x 175.9 x 80.0

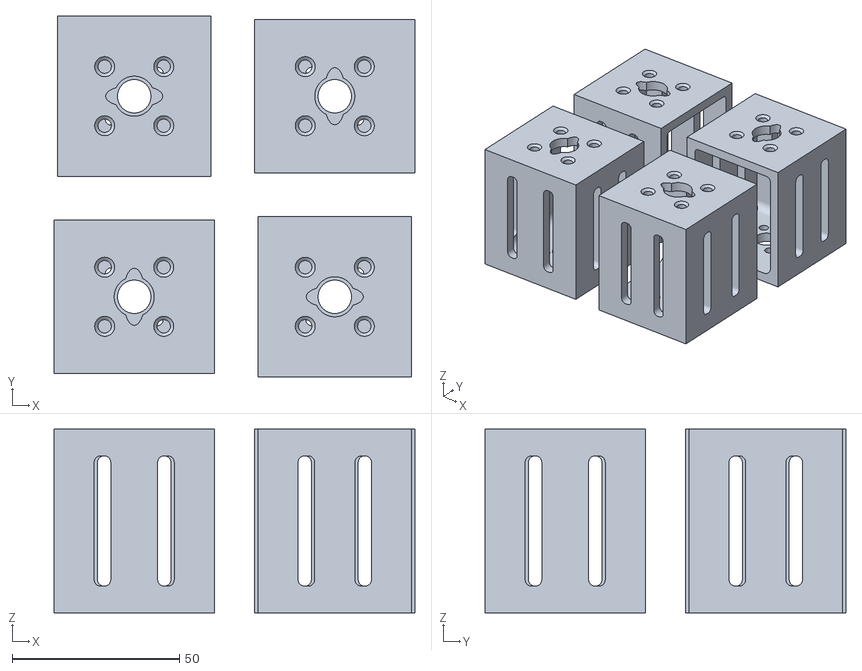
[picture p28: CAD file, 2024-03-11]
design/Parts_for_3D_printing_and_laser_cutting/Motor_stands/non_rotating_motor_stand_set v2.stl
108.0 x 108.0 x 55.0

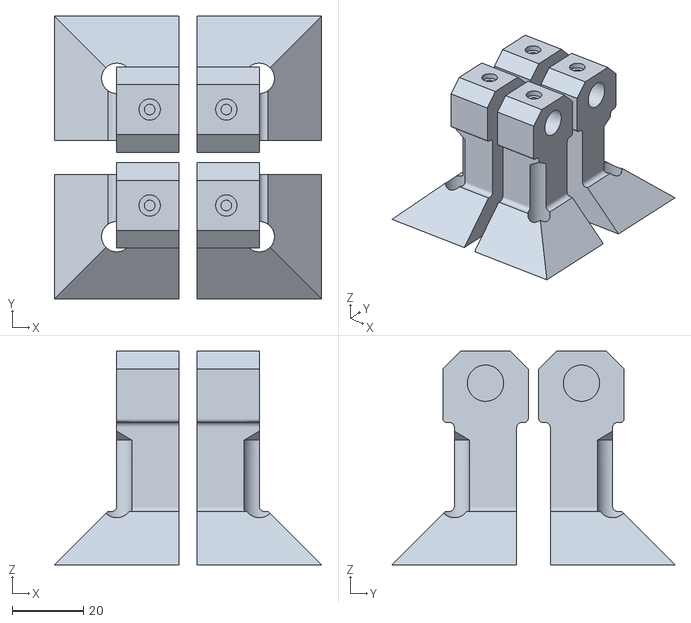
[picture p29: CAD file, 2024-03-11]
design/Parts_for_3D_printing_and_laser_cutting/Motor_stands/rotating_motor_stand_set v1.stl
75.0 x 79.4 x 60.0

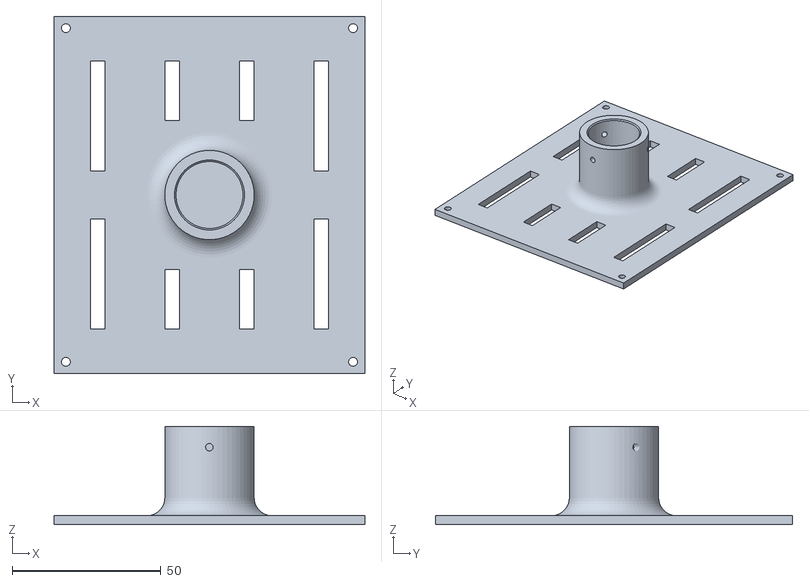
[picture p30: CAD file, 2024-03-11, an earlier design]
design/Parts_for_3D_printing_and_laser_cutting/Controller_case/Quadrotor_controller_case_lid v6.stl
104.4 x 120.0 x 33.0

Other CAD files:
design/Parts_for_3D_printing_and_laser_cutting/Propeller_guards/offset_propeller_guard v3.stl
design/Parts_for_3D_printing_and_laser_cutting/Motor_stands/rotating_motor_stand v1.stl
design/Parts_for_3D_printing_and_laser_cutting/Propeller_guards/symmetrical_propeller_guard v2.stl
design/Parts_for_3D_printing_and_laser_cutting/Propeller_guards/offset_propeller_guard v2.stl
design/Parts_for_3D_printing_and_laser_cutting/Anemometer_parts/Amemometer_case v6.f3d
design/Parts_for_3D_printing_and_laser_cutting/Controller_case/Quadrotor_controller_case v6.f3d
design/Parts_for_3D_printing_and_laser_cutting/Controller_case/Quadrotor_controller_case_lid v7.f3d
design/Parts_for_3D_printing_and_laser_cutting/GPS_and_antenna_parts/Base_station_adapter v7.f3d
design/Parts_for_3D_printing_and_laser_cutting/Motor_stands/non_rotating_motor_stand v12.f3d
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

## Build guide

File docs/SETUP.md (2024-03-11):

# Software Set Up
This documentation includes the relevant information on how to set up the software from scratch.

The following software has been tested on Raspberry Pi OS (32-bit) bookworm with Python 3.11.2 and pip 23.0.1. 

## Raspberry Pi OS
The Raspberry Pi OS can be installed on a USB stick or SD card by using the Raspberry Pi Imager as described [here](https://www.raspberrypi.com/software/).

We recommend using Raspberry Pi OS (32-bit) bookworm as it the most recent version we have tested on.

When switching on the Raspberry Pi for the first time there will be a short setup stage. For QUB students use the same password used for the other Raspberry Pi (if unsure ask a team member), for continuity across all our devices.

## Raspberry Pi Configuration
To be able to access the GPIO pins properly, the Pi must be configured.

First of all, if you haven't done so already, connect the Raspberry Pi to the Internet.

For QUB students see the image below. (This could take a few attempts)

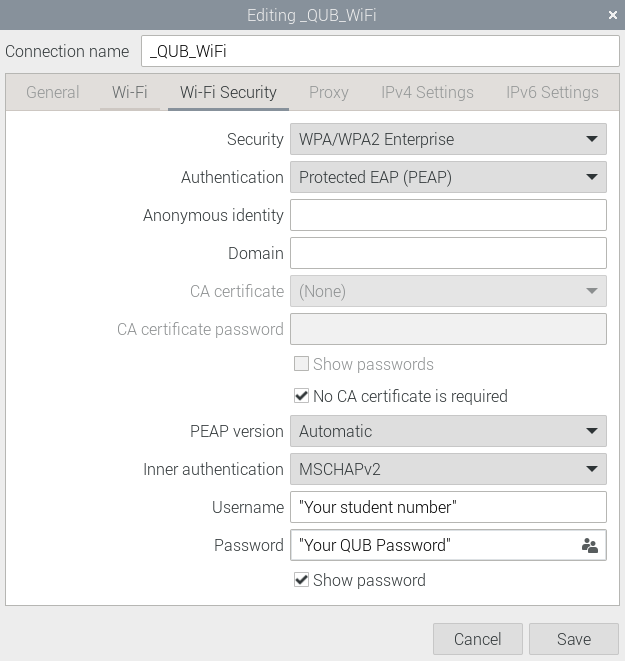
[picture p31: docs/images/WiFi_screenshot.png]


- Run the following
```
sudo raspi-config
```
- Select **3 Interface options**
- Select **4 I2C**
- Select **Yes**

* Select **3 Interface options**
*  Select **5 Serial port**
*  Select **No**
*  Select **Yes**

- Select **3 Interface options**
- Select **1 SSH**
- Select **Yes**

Next run
```
sudo nano /boot/firmware/config.txt
```
Add the following to the end of the file and save.
```
dtoverlay=uart2
arm_64bit=0
```
Then reboot with
```
sudo reboot
```

## Getting the code from GitHub
If you are looking to use our software, run the following 
```
cd ~
git clone https://github.com/QUB-ASL/bzzz.git
```
This will download all relevant source code into the folder `~/bzzz`.

## Setting up git to push (developers only)
This section is for collaborators only. Open a new terminal and carry out the following.

First, the user's name and email need to be added. This can be done by editing and running the following:
```
git config --global user.email "you@example.com"
git config --global user.name "Your Name"
```

Next you need to specify how to reconcile divergent branches.
```
git config --global pull.rebase true
```

Next an SSH key needs to be generated and added to the ssh-agent and GitHub account.

To generate an SSH key copy and paste the command below, substituting in your GitHub email address.
```
ssh-keygen -t ed25519 -C "your_email@example.com"
```
When prompted to "Enter a file in which to save the key", you can press Enter to accept the default file location.

When prompted to "Enter passpharse", just hit enter without providing a passphrase. When prompted to "Enter same passpharse again", hit enter again.

To add the SSH key to the ssh-agent run the following
```
ssh-add ~/.ssh/id_ed25519
```
for more information on Generating a new SSH key and adding it to the ssh-agent visit [here](https://docs.github.com/en/authentication/connecting-to-github-with-ssh/generating-a-new-ssh-key-and-adding-it-to-the-ssh-agent)

To add the SSH key to your GitHub account follow these [guidelines](https://docs.github.com/en/authentication/connecting-to-github-with-ssh/adding-a-new-ssh-key-to-your-github-account).

After all the above steps are complete run the following 
```
git clone git@github.com:QUB-ASL/bzzz.git
```

## Dependencies
There are a few packages that can not be installed in the virtual environment by `pip`, therefore should be installed system-wide. To install these dependencies, run:
```
sudo apt-get install libopenblas-dev libatlas-base-dev
```

## Virtual environment
All Python code is executed from within virtual environments. We use a virtual environment for the main Python code (e.g., radio interface, attitude control, etc) and a separate environment for the Discord Bots. Next a virtual environment can be created by (we have tested this with Python 3.11.2):
```
python -m venv venv_bzzz
```
For older versions of python use:
```
virtualenv -p python3 venv_bzzz
```

Then, activate the virtual environment:
```
source  venv_bzzz/bin/activate
```
and install the required packages:
```
cd bzzz/raspberry
pip install .
```

Now the `main.py` script can be run by:
```
sudo pigpiod
python main.py
```

## How to run the main Raspberry Pi code on start-up
After the virtual environment and dependencies have been installed as described above, a script can be used to automatically run the main Raspberry
Pi code on start-up.

To do this, the `run_main_on_start_up.sh` can be added to the users crontab by:

```
crontab -e
```
Then add the following:
```
@reboot sleep 10 && ~/bzzz/raspberry/run_main_on_start_up.sh
```

## Visual Studio Code
To install VS Code on Raspberry Pi run the following
```
sudo apt update
sudo apt install code
```
For more information visit [here](https://code.visualstudio.com/docs/setup/raspberry-pi).

After VS Code is installed, install the following extensions (these may take a while)
* Python
* PlatformIO

After the correct extensions are installed the ESP32 can be flashed. 

To do this, connect the ESP32 to the Raspberry Pi via USB then click the arrow in the top right corner or pressing Ctrl+Alt+U.

## How to remote access the Raspberry Pi using Visual Studio Code
It can be useful to access the Raspberry Pi from VS Code on your own device when testing or updating software onboard the quadcopter.

To do this:

* Install the 'Remote - SSH' extension on VS Code on your own device.
* Click on the blue and white inwards-facing arrows in the bottom left corner of VS Code.
* Click Connect to Host...
* Click + Add New SSH Host...
* If connected to _QUB_WiFi type in `ssh [username]@[hostname].qub.ac.uk`[^1]
* Alternatively you can use the username of the Pi followed by the IP Address of the Quadcopter[^2], e.g. `ssh bzzz1@123.456.789`.
* If asked, select the SSH configuration file you want to update.
* Click connect on the pop-up notification (right side of screen)
* When asked to select the platform of the remote host select `Linux`
* Enter the password for the Raspberry Pi

You are now ready to remotely edit the software onboard the quadcopter.

## Discord Bot 
QUB students should follow the [Discord Bot guidelines](../raspberry/DiscordBot) to be able to ssh into the Raspberry Pi.

## You are now ready to fly, go to [How to fly](../README.md#how-to-fly) 

[^1]: Remember you can use the [DiscordBot](../raspberry/DiscordBot) to find the Quadcopter's username and hostname
[^2]: Remember you can use the [DiscordBot](../raspberry/DiscordBot) to find the Quadcopter's IP Address

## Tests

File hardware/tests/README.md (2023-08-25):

# Hardware tests

## AHRS test
The AHRS hardware test tests the inertial measurement unit's Euler angles, 
quaternion angles and angular velocities. Copy and paste the `hw_test_ahrs.cpp` 
code into the `main.cpp`. Follow the instructions provided in the code to complete the hardware test.

## Motor test
The motor test has two modes the first of which runs the motors up to speed for 1 second
and then stops them for 1 second, this process is looped. The second test changes the PWM signal following a sinusoidal waveform.
Copy and paste the `hw_test_motors.cpp` file into the `main.cpp` to run the first test.
To run the second test comment out the first test and then uncomment the second one. 

## Motor and kill switch test
The motors in this test respond to throttle commands from the RC remote. Test requires the kill switch to be armed.
In this test the operator will hear a series of beeps from the buzzer:

| Beeps | Meaning |
| ----- | ---|
| 2 short | AHRS setup complete |
| 4 short | RC and Raspberry Pi connected |
| 2 long | preparation for arming |
| 6 short | Motors armed |
  
To run the test, copy and paste the `hw_test_motors_with_arm_kill.cpp` into `main.cpp`.

## Motor test with RC
In this test the motors respond to the throttle commands from the RC.
To run the test copy and paste the `hw_test_motors_with_receiver.cpp` into `main.cpp`.

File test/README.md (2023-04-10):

# Unit tests

This directory is intended for PlatformIO Test Runner and project tests.

Unit Testing is a software testing method by which individual units of
source code, sets of one or more MCU program modules together with associated
control data, usage procedures, and operating procedures, are tested to
determine whether they are fit for use. Unit testing finds problems early
in the development cycle.

More information about PlatformIO Unit Testing:

- https://docs.platformio.org/en/latest/advanced/unit-testing/index.html

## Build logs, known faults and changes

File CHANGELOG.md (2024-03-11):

# Change Log

All notable changes to this project will be documented in this file.

The format is based on [Keep a Changelog](http://keepachangelog.com/)
and this project adheres to [Semantic Versioning](http://semver.org/).

The following subsections are used:

- **Added**: new features
- **Fixed**: bug fixes
- **Changed**: other code changes

<!-- ---------------------
      v1.0.0
     --------------------- -->

## [v1.0.0] - 11 March 2024

### Added

- Timer interrupt ISR 
- New 3D printed parts 
- New Python interface for the barometer 
- Refuse to arm unless throttle stick is down and switches are at the correct positions
- Motors protocol when receiver gets disconnected 
- Create `ESC_calibration.cpp`
- Read data from Terabee TOF sensor
- Read anemometer data in background; Read and save anemometer data on Pi
- Update logo
- Discord bots and documentation ; run the DiscordBot client and Raspberry Pi main script on start-up
- Parser of NMEA messages from GNSS module

### Fixed

- Correct import names
- Documentation issues and typos
- Update `setup.py` and `platformio.ini`
- Update `README.md`
- Fix typos in `ahrs.hpp`

### Changed

- Update SETUP.md for remote access
- Update maximum attitude gains from trimmers and attitude gains
- Improve docs in `read_sbus_from_GPIO_receiver.py`
- Update ESC and buzzer pins 
- Update issue bug_report
- Update PCB's

<!-- ---------------------
      v0.2.0
     --------------------- -->

## [v0.2.0] - 28 August 2023

### Added

- First implementation of altitude hold mode.
- Data logging on Raspberry Pi (data is saved in CSV file).
- A fail-safe to shut down the drone when the receiver connection is timed-out due to a possible loss of connection.
- Yaw rate controller.
- Schematics for electronic board with ESP32.

### Fixed

- Fixed the unnecessary yawing of the drone (the drone now yaws only when commanded)
- Packaged Python code
- Fixed incompatibility between ThreeWaySwitch and bit shift operator

### Changed

- Communication protocol between ESP32 and Raspberry Pi

<!-- ---------------------
      v0.1.0
     --------------------- -->
## [v0.1.0] - 1 June 2023

### Added

- Average initial attitude computed in AHRS (see `averageQuaternion`)
- Calibrate with initial angular velocities
- Check arming switch in setup
- Check kill switch in loop
- Disarm and exit loop if killed
- Clip signals to motors
- Wait for Raspberry Pi to send data over serial

### Fixed

- Removed hard-coded magnetometer and other parameters from `main.cpp`
- Deactivate all printing while flying
- Significant fix for arming issue (new communication protocol between RPi and ESP32)

### Changed

- Change all `Serial.print` to `logSerial`
- Delete `config.cpp`
- Rename `BZZZ_VERBOSITY` to `BZZZ_LOGGING_LEVEL`
- `logSerial`, `setupBuzzer`, `buzz` and `waitForPiSerial` go to `util`
- Update hardware tests

[v1.0.0]: https://github.com/QUB-ASL/bzzz/releases/tag/v1.0.0
[v0.1.0]: https://github.com/QUB-ASL/bzzz/releases/tag/v0.1.1
[v0.2.0]: https://github.com/QUB-ASL/bzzz/releases/tag/v0.2.0

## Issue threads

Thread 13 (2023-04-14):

Implement LQR controller framework

alphaville, 2023-04-14:
Implement LQR controller framework

alphaville, 2023-04-19:
This is being addressed in #16. We should also create a timer interrupt (see [§4.2](https://github.com/QUB-ASL/bzzz/blob/main/CONTRIBUTING.md#42-memory-shared-between-isr-and-loop) of the contributing guidelines).

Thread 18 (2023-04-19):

Bash script to run Python script

alphaville, 2023-04-19:
Create a bash script that will: (i) activate the virtual environment, (ii) run the Python scirpt that reads from the RC and sends reference data to the ESP32. Make sure that the script is executed at startup.

alphaville, 2023-04-20:
Completed

alphaville, 2023-04-20:
@jamie-54 we should probably include some documentation somewhere (e.g., a README file in `hardware/docs`) on how to set up the cron job.

alphaville, 2023-08-22:
I'm re-opening this issue. @gunturiCM can you take care of this?

alphaville, 2023-09-05:
@jamie-54 we have a script on RPi. Can you put it here and make a PR?

alphaville, 2023-09-11:
@jamie-54 any progress on this?

jamie-54, 2023-09-11:
looking into it now

Closed 2023-10-27.

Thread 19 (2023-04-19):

Relative attitude with respect to initial attitude

alphaville, 2023-04-19:
The attitude of the quadcopter should be taken with respect to its attitude at time zero, that is, if the initial quaternion is $q_0$ and the currect quaternion is $q_t$, we should consider the attitude of the quadcopter to be $\tilde{q}_t = q_t \ominus q_0$.

alphaville, 2023-04-20:
- I tested this and noticed that the initial quaternion turns out to be something like $q = (0, 0, 0, 1.7)$, which is far from being a unit quaternion
- I had some issues for a while due to my IMU not being properly calibration
- I will test our implementaiton of `Quaternion` to make sure we don't have any bugs there

alphaville, 2023-04-21:
Done and tested

Closed 2023-04-21.

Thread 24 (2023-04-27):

Possible bug in Attitude Error

jamie-54, 2023-04-27:
When the `m_quaternionGain` is increased it makes one of the motors spin faster while the rest remain still.

By increasing the `PITCH_MAX_RAD` in `config.hpp` it made it more noticeable.

I've tried to do some debugging over the last few days but its still present.

First I checked the control actions to the motor equations (end of `main.cpp`) and they where correct.

When the `referenceQuaternion` is set to (0,0,0) it seems to go away.

I checked the `quaternion.cpp` file and the quaternion from NED Euler angles is correct.

I then checked the `mapRadioToAngle` function in the `radio.cpp` and the formula correct therefore I can't see anything wrong with the  `referenceQuaternion`.

I also printed the `relativeQuaternion` and it seemed to be behaving correctly so I'm not sure what the issue is, was thinking maybe its something to do with subtracting one quaternion from the other, but not sure.

jamie-54, 2023-05-02:
**Issue resolved**
Issue was `mapRadioToAngle` function in `radio.cpp` file

Closed 2023-05-02.

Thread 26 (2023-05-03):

Clipping of signals to the motors

alphaville, 2023-05-03:
Following up from #24, we figured out that the error was related to the calculation of the pitch and roll angles using `mapRadioToAngle`. I guess the issue was that we would send a very low value to the motors, so we would effectively disarm them.

I guess it is safer to apply some clipping to the signals we send to the motors to make sure they remain within the desired bounds

Closed 2023-05-09.

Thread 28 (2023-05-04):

ESCs not arming/functioning properly

alphaville, 2023-05-04:
The ESCs sometimes don't arm or don't function properly and then we have to reset the ESP32.

alphaville, 2023-05-04:
[This guy here](https://youtu.be/ce81bDdOn0M) is suggesting to arm by increasing the throttle *gradually* from a low value to a higher one until the motors start to spin.

alphaville, 2023-05-04:
More interestingly, [this guy](https://youtu.be/obR5Gky3sms) says that some ESCs may refuse to arm - or will behave weird - if they are powered, but it takes a long time to arm. In our `setup` function, `setupMotors` is called last. Maybe it should be first (after we beep the buzzer a couple of times to warn the operator).

jamie-54, 2023-05-05:
Hi, we could check if the first video works.
Just checking I thought we didn't want to arm the motors until the Arm switch was used?
In which case we have to wait more than 20s for the Pi script to work.
The second video seems to imply that we shouldn't have an arm switch, it should just arm when the quadrotor is switched on.
We could do this and just work with one on-off switch?

alphaville, 2023-05-05:
Oh, yes, you're right. Moreover, the operator may simply want to arm the ESCs after some time. Did you try the first solution?

alphaville, 2023-05-09:
@jamie-54 if the problem hasn't been resolved we should ask a question at one of the following channels:

- [Electronics SE](https://electronics.stackexchange.com/)
- [r/Multicopter/](https://www.reddit.com/r/Multicopter/) on Reddit
- [RC_ESC on GitHub](https://github.com/RB-ENantel/RC_ESC?utm_source=platformio&utm_medium=piohome)

alphaville, 2023-05-11:
That's excellent - we're narrowing it down...

gunturiCM, 2023-05-31:
This has been fixed and addressed in #52 .

alphaville, 2023-06-01:
Reopening because the PR has not been reviewed/merged

gunturiCM, 2023-06-01:
This has been fixed and addressed in #52 and the fix has been approved now.

Closed 2023-06-01.

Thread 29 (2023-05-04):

Fail safes

alphaville, 2023-05-04:
Implement the following safety measures (these are common safety measure I've found online):

- [x] **Arm switch:** the motors will not arm unless the arm switch is flipped
- [x] **Kill switch:** the kill switch kills the motors
- [x] **Buzzer:** the buzzer makes a sound before arming (or re-arming) and after disarming
- [x] **Lost connection:** they say that if the copter looses connection, it should shutdown immediately

jamie-54, 2023-05-05:
Hi, the arm and kill switch are working but we might want to modify them.
Currently switch B Arms the motors and switch A can stop and start the motors.
The buzzer is connected to GPIO 27 so we could probably make a function for it.

alphaville, 2023-05-05:
@jamie-54 has this been pushed? I don't see anything here.

jamie-54, 2023-05-05:
yea in the `main.cpp` of the `feature/flight-zero` branch. It looks like some parts didn't merge into the `dev` and `main` branch

alphaville, 2023-05-05:
That's not possible. Actually I had a look at `feature/flight-zero` before we merged it and the fail safes weren't there. I thought you wanted to introduce them later. If you have the code locally, can you push it to a new branch out of `dev` and open a PR?

jamie-54, 2023-05-06:
Actually if we look at the [network graph](https://github.com/QUB-ASL/bzzz/network) we can see where things went a bit funny. The correct code seems to be showing in the [`main.cpp`](https://github.com/QUB-ASL/bzzz/blob/feature/flight-zero/src/main.cpp) of  the `feature/flight-zero` branch, lines 130-135 is the arming and lines 146-154 is the kill switch. I'll create a PR now and it should sort it out, thanks

Closed 2023-07-06.

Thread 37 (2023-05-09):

Create timer interrupt

alphaville, 2023-05-09:
We may need to create an ISR or two. In principle it is good practice.

alphaville, 2023-08-22:
bump @jamie-54 @gunturiCM

alphaville, 2023-09-08:
bump @jamie-54

alphaville, 2023-10-16:
bump @jamie-54

alphaville, 2024-01-18:
@Runway27, @pdavid747, @ejb-11, @Yuanbwcx, @Minanchi, please let me know if you can take care of this issue.

Runway27, 2024-01-18:
Sir, what exactly has to be done in this? I'm unable to understand the issue.

alphaville, 2024-01-18:
If you see our code in [`src/main.cpp::loop`](https://github.com/QUB-ASL/bzzz/blob/dev/src/main.cpp#L77), we have just put all functionality in the `loop` function. The rate at which `loop` runs is not fixed. It is standard practice to use an interrupt service routine (ISR) to guarantee that the loop function runs at a fixed rate.

I have written some few comments on this in [`CONTRIBUTING.md`, Section 4](https://github.com/QUB-ASL/bzzz/blob/main/CONTRIBUTING.md#4-esp32-specific-details).

alphaville, 2024-01-20:
Here is a little example of using a timer to make an LED blink at a desired frequency:

```c
#include <Arduino.h>

#define TIMER_ID 0
#define TIMER_PRESCALER 80
#define LED_PIN 14
#define TIMER_INTERVAL_uS 1000000

hw_timer_t *timer = NULL;
portMUX_TYPE timerMux = portMUX_INITIALIZER_UNLOCKED;

/**
 * Here the timer state is declared as a global variable
 * so that it can be accessed by the loop function (and possibly
 * by other interrupts). When accessing `timerState` we should
 * be first acquiring its lock (i.e., the `timerMux`).
 */
volatile bool timerState = true;

/**
 * Callback, attached to the timer interrupt
 * It is generally advisable to keep the implementation of this
 * function as lean as possible (it should just toggle a flag).
 * This function is executed only ONCE every period.
 */
void IRAM_ATTR onTimer()
{
  taskENTER_CRITICAL_ISR(&timerMux);
  timerState = !timerState;
  taskEXIT_CRITICAL_ISR(&timerMux);
}

void setup()
{
  pinMode(LED_PIN, OUTPUT);

  timer = timerBegin(TIMER_ID, TIMER_PRESCALER, true);
  timerAttachInterrupt(timer, &onTimer, true);
  /*
   * timerAlarmWrite is simply a counter; we count a number of
   * timer periods before calling the callback function (onTimer).
   * The second argument is the sampling period in micros.
   */
  timerAlarmWrite(timer, TIMER_INTERVAL_uS, true);
  timerAlarmEnable(timer);
}

/**
 * Unlike the callback function (onTimer), the loop function
 * runs continuous and is therefore executed several timer
 * per period.
 */
void loop()
{
  taskENTER_CRITICAL_ISR(&timerMux);
  digitalWrite(LED_PIN, timerState);
  taskEXIT_CRITICAL_ISR(&timerMux);
}
```

@Runway27 @ejb-11 @jamie-54 @Yuanbwcx @Minanchi @pdavid747 This issue hasn't been assigned to anyone. Please let me know who can take care of it. If you have questions, I'll be happy to discuss.

alphaville, 2024-01-20:
On a side note, I've seen the following simpler approach being proposed here and there:

```c
#include <Arduino.h>

#define LED_PIN 14
#define TIMER_INTERVAL_uS 1000000

const int samplingPeriodMs = 1000; // in ms
unsigned long startTime;
bool timerState = true;

void setup()
{
  pinMode(LED_PIN, OUTPUT);
  digitalWrite(LED_PIN, LOW);
  startTime = millis(); // Initialize
}

void loop()
{
  // Now the execution is controlled by `millis()`
  if (millis() > startTime + samplingPeriodMs)
  {
    digitalWrite(LED_PIN, timerState);
    timerState = !timerState;
    startTime = millis();
  }
}
```

The problem with this is that it won't work for low sampling periods because `millis` is not very accurate - the same goes for `micros`.

Runway27, 2024-01-20:
Sir, I have quite a few open issues currently. Probably after finishings a few this week I can subscribe to this.

Closed 2024-02-19.

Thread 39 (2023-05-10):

Update hardware tests (motors)

jamie-54, 2023-05-10:
Update hardware test for motors with and without arm/kill switches and receiver
* `hw_test_motors.cpp`
* `hw_test_motors_with_receiver.cpp`
* `hw_test_motors_with_arm_kill.cpp`

jamie-54, 2023-05-25:
Hardware test for motors have been updated and merged

Closed 2023-05-25.

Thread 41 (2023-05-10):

Tidy up main.cpp

jamie-54, 2023-05-10:
Remove functions from the top (above `setup`) of  `main.cpp` and put them in their correct files.

jamie-54, 2023-05-10:
Should the likes of `setupMotors` be in the `motors.cpp`?
What's your thoughts @alphaville @gunturiCM ?

alphaville, 2023-05-10:
@jamie-54 sounds reasonable. Also `buzz` could go into a file with utility functions. Should this be `config`?

alphaville, 2023-05-10:
@jamie-54 have a look at #45

jamie-54, 2023-05-10:
> @jamie-54 have a look at #45

will do thanks

jamie-54, 2023-05-11:
Issue resolved

Closed 2023-05-11.

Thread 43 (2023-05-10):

Angular velocities bias (add Initial angular velocities)

jamie-54, 2023-05-10:
After the `preflightCalibrate` there still seems to be a slight bias in the angular velocities.
As a work around we can determine the `initialAngularVelocity` and subtract these from the `measuredAngularVelocity`

alphaville, 2023-05-24:
Haven't we done this already? By the way, if the Madgwick filter works properly there shouldn't be a constant bias.

alphaville, 2023-05-24:
A little bit of bias will not cause any issues, but I wonder why it's not zero at rest. Maybe @gunturiCM could come up with an [MRE](https://en.wikipedia.org/wiki/Minimal_reproducible_example) and create an issue on the GitHub page of the Madgwick library we use.

jamie-54, 2023-05-24:
Yea think the easiest way to show the error is to copy `hw_test_ahrs.cpp` into `main.cpp` and uncomment *TEST TO CHECK ANGULAR VELOCITIES* and use Arduino ide to plot the angular velocities.

gunturiCM, 2023-05-28:
I will try to reproduce the error.

# This is for my future reference
1. It is to be noted that on page 12 of the [register map](https://invensense.tdk.com/wp-content/uploads/2015/02/MPU-9250-Register-Map.pdf) document mentions that the stored offsets will be automatically deducted before the gyro data is written to the sensor data registers. The `preFlightCalibrate` stores the calculated offset in the corresponding offset registers.
2. The `preFlightCalibrate` function calculates the offsets at gyro full-scale as 250 degrees/s and accelerometer full-scale as 2g, we are using a different scale. Assuming the DC bias is dependent on the selected scale, this could be causing the issue. At the time of writing this, I couldn't find any evidence to back this assumption. This needs to be investigated.

gunturiCM, 2023-05-31:
I did the following tests, while the IMU remained stationary:
1. Without changing anything I have printed the raw measurements from the gyro. The bias in these measurements seems to be around 1.1 degrees/s. Let us call this _raw bias_.
2. I have manually set the bias values to zero before the function `preFlightCalibrate` writes them to the EEPROM. I thought that the bias in the raw measurements will change, but they didn't. They actually were the same as the _raw bias_. This either means that the biases were not automatically deducted from the measurements, or this bias couldn't be compensated for.
3. I have changed the gyro settings used in `preFlightCalibration` to what we are using while operating the drone. This did not fix anything. The output was the same as _raw data_.
4. I have changed the gyro settings used while operating the drone to what we are using in `preFlightCalibration`. This did not fix anything. The output was the same as _raw data_.
The above two tests showed that this bias is independent of the full-scale selections of the gyro.
The resulting bias is 1.1 dps is extremely low, 1.1*100/2000 = 0.055%, which if I am interpreting the [datasheet section 3.1]{https://invensense.tdk.com/wp-content/uploads/2015/02/PS-MPU-9250A-01-v1.1.pdf} correctly, is with-in the expected error range.

## **With this, I think that this might be an imperfection in the product rather than a software issue.**

alphaville, 2023-05-31:
@gunturiCM try a different IMU to see if it's a possible hardware issue

alphaville, 2023-07-06:
@gunturiCM shall we close this?

Closed 2023-07-26.

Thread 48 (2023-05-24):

Possible issues with reading data from RPi

alphaville, 2023-05-24:
This is how we read the data from the Raspberry Pi:

```c++
String allDataFromPi;
if (Serial.available() > 0) {
    allDataFromPi = Serial.readStringUntil('\n');
    for (int i = 0; i < 16; i++) {
         m_channelData[i] = allDataFromPi.substring(1, allDataFromPi.indexOf(",")).toInt();
         allDataFromPi = allDataFromPi.substring(allDataFromPi.indexOf(",") + 1);
    }
}
```

There may be some issues here:

- When we start to read data from the Pi, we may start to read a line mid way, so we will not read all 16 numbers. A possible solution can be to put a certain character at the beginning of every message (e.g., `M` or something)
- It is not impossible that the Pi sends garbage data every now and then.
- We can try to increase the baud rate. The Pi supports baud rates up to 2M. The ESP32 can allegedly go up to 5M, although some users have reported issues above 2M. I would try 500,000.
- We can decrease the size of the message. We can encode the state of the switches as 0/1.

gunturiCM, 2023-05-31:
The suggestions have been adapted and tested in #52. After testing, no issues were found. Closing this issue.

alphaville, 2023-06-01:
Reopening because the PR has not been reviewed/merged

Closed 2023-06-01.

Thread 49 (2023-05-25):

Delete Branches

jamie-54, 2023-05-25:
Hi, I see we have a view branches that seem to be out of date or not used anymore.
Should we delete them to keep the repo tidy?

alphaville, 2023-05-26:
Of course. I deleted a few. We now have only `main`, `dev`, and `feature/arm-kill`, which hasn't been merged and seems to be a little old.

jamie-54, 2023-05-26:
I think `feature/arm-kill` can be deleted as well since we have the arm and kill switches working

Closed 2023-05-26.

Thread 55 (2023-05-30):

Throttle capping

jamie-54, 2023-05-30:
Just a quick point, we cap the throttle in the code and on the remote.
Do we need both?
It works with both but just thought I'd make us all aware this is what we are doing.

gunturiCM, 2023-05-31:
I think it is a good idea to cap it in the code regardless of the setting on the remote.

alphaville, 2023-07-26:
Folks, do we still need this issue?

jamie-54, 2023-07-26:
No closing now

Closed 2023-07-26.

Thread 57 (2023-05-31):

Board re-design

alphaville, 2023-05-31:
I've created this issue to keep track of the re-design of the board. Feel free to comment. Some notes:

- We'll keep the boards separately and they'll be connected by a USB cable
- We need to figure out how to power both boards neatly (Will the ESP be powered via the USB cable?)
- The OS on RPi will be on a USB stick
- Put four holes on the board; we can use screws and spacers to keep the RPi and our board (with the ESP32) together

We should also keep the grb files (and a PNG version) on GitHub. Share your throughs below.

## TODOs

- [x] Initial electric schematic (prepare and contribute to GitHub)
- [x] Review of initial schematic
- [x] Create Gerber file for PCB
- [x] Compile list of components to purchase

Until then, let us modify the existing board

alphaville, 2023-05-31:
@jamie-54 @gunturiCM Meanwhile, as we discussed yesterday, let us use the current version of the board and cut the UART connection between the RPi and the ESP.

alphaville, 2023-05-31:
@jamie-54 @gunturiCM I cut the serial connection between the RPi and the ESP (see on the left). The board should work now if we use a USB cable and a USB stick.

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

alphaville, 2023-05-31:
Also, if we use the cable it would be good to rotate the ESP32 so that the two USB ports are one the same side

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

alphaville, 2023-06-01:
> Professor, I think it is a better idea to make a proper schematic first rather than designing the PCB directly. When we have everything needed on the board, we will start designing the PCB. It is standard practice to make the schematic first. The ESP can be powered by the native USB port.

Chandra, could you take the lead and make a first draft of the schematic?

Closed 2023-07-06.

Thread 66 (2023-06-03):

Yaw control from the RC

alphaville, 2023-06-03:
Let us re-introduce the following line in [`main.src`](https://github.com/QUB-ASL/bzzz/blob/main/src/main.cpp#L94)

```c++
yawReferenceRad += radio.yawRateReferenceRadSec() * SAMPLING_TIME;
```

But,

- Make sure `radio.yawRateReferenceRadSec() ` is zero unless we move the left stick; equivalently,
- `yawReferenceRad` doesn't drift unnecessarily
- Make sure the magnitude of the values of `radio.yawRateReferenceRadSec()` are reasonable (experimentation will be needed)

gunturiCM, 2023-06-07:
I have opened another _experimental_ branch to see if we can use the `yawRateReference` to control the `Yaw` and have the `yawreference = currentYaw`.

gunturiCM, 2023-06-09:
This has been addressed and solved in #71. The code was tested and successfully merged.

Closed 2023-06-09.

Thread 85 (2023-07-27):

BNO055 (Adafruit) IMU Sensors

jamie-54, 2023-07-27:
Implement new IMU code to read and process data from BNO055 on ESP.

- Create a hardware test for BNO055.

Closed 2023-12-05.

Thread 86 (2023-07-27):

BMI088 (Bosch) IMU Sensors

jamie-54, 2023-07-27:
Implement new IMU code to read and process data from BMI088 on ESP.

- Create a hardware test for BMI088.

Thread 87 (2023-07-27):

Read Anemometer Data on Pi

jamie-54, 2023-07-27:
Anemometer is working with the TriSonica User App which can be downloaded [here](https://anemoment.com/resources/).

## Things to do
- Interface Anemometer with Raspberry Pi

Closed 2023-11-23.

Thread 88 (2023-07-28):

Sensor board design for BMI088

boyle26, 2023-07-28:
New board sensor board design replacing the older VL53L0X IMU with the Bosch BMI088. This will include:
- Schematics
- Board layouts
- Gerber files

Waiting on test results to determine which IMU to move ahead with design. No point seen in designing two boards with if only one will be used.

alphaville, 2023-11-23:
@jamie-54 I suppose we can close this, right?

jamie-54, 2023-11-23:
yea

Closed 2023-11-23.

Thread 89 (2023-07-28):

Sensor board design for BNO055

boyle26, 2023-07-28:
New board sensor board design replacing the older VL53L0X IMU with the Bosch BNO055. This will include
-Schematics
-Board layouts
-Gerber files

Waiting on test results to determine which IMU to move ahead with design. No point seen in designing two boards with if only one will be used.

alphaville, 2023-11-23:
@jamie-54 shall we close this?

jamie-54, 2023-11-23:
yea

Closed 2023-11-23.

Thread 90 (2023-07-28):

Fix mounting hole alignment on VL53L0X sensor board

boyle26, 2023-07-28:
Mounting holes on board do not line up with holes on the drone's fuselage. Board layout and gerber files need changed to correct this issue

Closed 2023-08-01.

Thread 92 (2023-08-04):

Sensor board missing SCL trace

boyle26, 2023-08-04:
Sensor board serial clock pins SCL are not connected to the HDMI.

jamie-54, 2023-08-17:
@boyle26 has fixed this issue so closing it now

Closed 2023-08-17.

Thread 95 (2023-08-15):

ESC calibration

jamie-54, 2023-08-15:
Create a function for calibrating the ESC's using the ESP32.

Include a readme explaining how to carry out the calibration

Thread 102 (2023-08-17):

3D Printed parts

jamie-54, 2023-08-17:
Add a folder to keep 3D printed files

Upload relevant files

alphaville, 2023-08-17:
@jamie-54 @gunturiCM @boyle26 who has the files?

jamie-54, 2023-08-21:
I have the most recent stl files

Closed 2023-10-27.

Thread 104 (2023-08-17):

ESP32 board: changes needed

alphaville, 2023-08-17:
The following changes are needed on the ESP32 board:

- We need to correct the dimensions of ESP32 (now it is too narrow)
- Add four pull-down resistors at the ESC signals
- Proposal: connect the buzzer both to the ESP32 and the Pi using diodes

jamie-54, 2023-11-30:
@alphaville this can be closed?

Closed 2023-11-30.

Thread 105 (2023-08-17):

README files

alphaville, 2023-08-17:
- [x] The main readme file is meant to offer general information about the project and signpost the user to the documentation. The hardware schematics don't belong there. The main readme file should explain the structure of the project. In other words, "what are all these folders you have here?!", the user will ask. The main readme file should also point to `CONTRIBUTING.md` and `SAFETY.md`
- [x] Create a readme file [here](https://github.com/QUB-ASL/bzzz/tree/dev/design/PCBs) to describe the schematics. @gunturiCM it would be good to include a schematic that shows how the different boards are connected. And a few photos too.
- [x] The folder [`raspberry`](https://github.com/QUB-ASL/bzzz/tree/main/raspberry) and it sub-folders should have a readme file (every Python package needs a main readme file)

alphaville, 2023-08-22:
bump @gunturiCM @jamie-54

gunturiCM, 2023-08-23:
I will come back to update the schematics as per the suggestions as I write my report. Thanks professor.

Closed 2023-08-25.

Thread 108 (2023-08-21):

Implementation of `ESP` data checking in `process_ESP_data` in `main.py`.

gunturiCM, 2023-08-21:
In reference to ` Why don't you make an issue about this? Otherwise, we'll forget.`

_Originally posted by @alphaville in https://github.com/QUB-ASL/bzzz/pull/107#discussion_r1300013837_

This issue is opened to remind that, in function `process_ESP_data` in `main.py`, we are casting received UART data from `ESP` to `floats`. There was no check for data corruption implemented before casting.

There should be an additional check for data corruption to prevent program crashes.

gunturiCM, 2023-08-21:
This has been resolved in #107.

Closed 2023-08-21.

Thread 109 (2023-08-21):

Some concerns about read_sbus_from_GPIO_receiver.py

alphaville, 2023-08-21:
My concerns:

- The file name doesn't correspond to the contents. Should probably be `rc_parser` or `rc_reader`
- This is currently not an RC reader - it's an RC-read-and-sender-to-ESP - a **relay** one may say; however, it's best to have an `RCReader` class and an `EPSTransmitter` (or how you want to call it) to send data to the ESP. Now it is too convoluted
- Documentation is needed

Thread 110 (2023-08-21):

Refuse to fly unless the switches are at the correct positions

alphaville, 2023-08-21:
Additional safety measure: The quadcopter should refuse to fly when the script starts unless the switches are at the correct positions (A: up, B: up, C: first position, D: down) **and** the throttle stick is fully down. In fact the buzzer should make a sound. Since we can control the buzzer only from the ESP, it should be good to implement this on the ESP.

alphaville, 2023-08-22:
@gunturiCM will you take care of this?

alphaville, 2023-11-29:
@jamie-54 @Yuanbwcx @Runway27 @pdavid747 @Minanchi We should take care of this issue before we start flying again to avoid accidents! Who can take care of this?

alphaville, 2023-11-30:
@jamie-54 @Yuanbwcx @Runway27 @pdavid747 @Minanchi folks, I still haven't received any replies from you on this. Who can take care of this issue?

jamie-54, 2023-11-30:
me and @Runway27 can look at this tomorrow

alphaville, 2024-01-18:
@jamie-54 and @Runway27 - should we close this issue?

Runway27, 2024-01-18:
Yes sir, this issue has been resolved. But the PR regarding this has issue #165 which is to be resolved.

alphaville, 2024-01-18:
Indeed, PR #172 is addressing two issues (#110 and #165), but this is not good practice. A PR should aim to close one issue (even when it partly addresses multiple ones). In any case, #172 still has unresolved conversations and has not been approved.

I suggest we make PR #172 address only #110, we then review it quickly, we merge it, and we open a PR to work on #165. Does this work, @Runway27 and @jamie-54?

Runway27, 2024-01-18:
Yes sir, we can do that.

jamie-54, 2024-01-18:
> Indeed, PR #172 is addressing two issues (#110 and #165), but this is not good practice. A PR should aim to close one issue (even when it partly addresses multiple ones). In any case, #172 still has unresolved conversations and has not been approved.
>
> I suggest we make PR #172 address only #110, we then review it quickly, we merge it, and we open a PR to work on #165. Does this work, @Runway27 and @jamie-54?

Sounds good

Runway27, 2024-01-29:
Are we happy to close this issue?

jamie-54, 2024-01-29:
> Are we happy to close this issue?
Yea sounds good to me

Closed 2024-02-05.

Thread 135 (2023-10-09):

Updated PCB's

jamie-54, 2023-10-09:
### Describe the solution you'd like

## ESP Board
- [x] fix ESP pin layout
Consider new IMUs

## Pi Board
- [x] Add buzzer
- [x] Add slot for HDMI
- [x] Add Anemometer header

## Sensor Board
- [x] fix (swap) VL53L0X time of flight sensor SDA and SCL port
- [x] Add TeraBee time of flight sensor

alphaville, 2023-11-15:
@jamie-54 are there any other updates we need? Is #136 ready for review?

Closed 2023-11-21.

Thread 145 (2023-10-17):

numpy version in setup.py

jamie-54, 2023-10-17:
### Describe the bug

when trying to run `main.py` there is a numpy error

### Affected File

main.py  (setup.py)

### Affected Line

_No response_

### To Reproduce

` python raspberry/main.py`

### Minimum reproducible example

```

python raspberry/main.py

```

### Additional context

older version of numpy works

Closed 2023-10-26.

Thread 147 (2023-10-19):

pigpio already installed

jamie-54, 2023-10-19:
### Describe the bug

I'm pretty sure the new Raspberry Pi OS (`bookworm`) comes with `pigpio` pre-installed.

This can be removed from the setup.py file.

### Affected File

raspberry/setup.py

### Affected Line

39

### To Reproduce

N/A

### Minimum reproducible example

N/A

### Additional context

_No response_

Closed 2023-10-26.

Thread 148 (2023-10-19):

bash script for Discord Bot on start up

jamie-54, 2023-10-19:
### Describe the solution you'd like

Create a bash script that will run the `raspberry/DiscordBot/main.py` file on start up

Closed 2023-10-27.

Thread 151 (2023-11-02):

Logo Makeover

ethetic, 2023-11-02:
### Describe the issue

The current logo has clipping and is pixelated when zoomed close.
How about this SVG where it is cleaned up?

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

### Affected File

README.md

### Affected Line

--

alphaville, 2023-11-02:
Thank you, @ethetic. This looks a lot better. Could we get rid of the pacifier?

jamie-54, 2023-11-02:
Thanks @ethetic, it looks better than are current version. I'm happy to update it, what's your thoughts @alphaville?

Closed 2023-11-07.

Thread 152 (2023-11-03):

Suspected typo

jamie-54, 2023-11-03:
### Describe the issue

Think there is a typo, or we should change the variables name, you'll see.

### Affected File

raspberry/bzzz/main.py

### Affected Line

194 and 199

alphaville, 2023-11-06:
What is the typo? Can you paste the code here?

jamie-54, 2023-11-07:
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

throttle in line 189 as well

jamie-54, 2023-11-16:
can do

Closed 2023-11-16.

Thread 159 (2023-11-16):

RFC: Configuration sequence from RPi to ESP32

alphaville, 2023-11-16:
### Describe the solution you'd like

### The issue

We have currently hard-coded certain parameters in the ESP32 code. For example:

- The magnetometer scaling factors and offsets are hard-coded
- The assignment of the tuning knobs is fixed (e.g., VRB, VRC, VRD are currently the attitude control gains, but later we will need to ressign them to other parameters)

and there might be other such hard-coded values. It would be better to be able to configure them from the Pi.

### Proposed solution

The Pi will send via the Serial an initialisation sequence. In particular, it will send out the message in JSON format

```json
{"command": "initialisation"}
```

in a while loop until the ESP32 reads it and acknowledges it by replying

```json
{"status": "initialisation"}
```

Then, the Raspberry Pi will send to the ESP one the following messages

#### Proceed

if the ESP should just proceed with the default parameters, the following command should be issued
```json
{"command": "proceed"}
```
The ESP should then acknowledge this by sending back the message
```json
{"status": "proceeding"}
```

#### Calibrate

The Pi can send the command to the ESP for it to calibrate the magnetometer
```json
{"command": "calibrate" }
```
The ESP will then acknowledge the message by saying `{"status": "calibrating"}` and once it has calibrated the magnetometer it will say `{"status": "calibration complete"}`.

#### Set gains

The following command can be sent to set certain (fixed) values to any of the controller gains or other parameters
```json
{
    "command": "set_gains",
    "gain_xy": 123.4,
    "gain_omega_xy": -5.67
}
```
Again, the ESP will acknowledge the receipt of the command with `{"status": "setting gains"}` and
```json
{
   "status": "gains set by RPi",
    "gain_xy": 123.4,
    "gain_omega_xy": -5.67,
    "gain_omega_z": 1.0101,
    "other_parameter": 0.5
}
```

#### Arming

When the ESP is ready to arm, it should return the message:
```json
{"status": "ready to arm"}
```
before it arms, it should inform the Pi by sayin
```json
{"status": "arming"}
```
and when it arms, it should say
```json
{"status": "armed"}
```

#### Assignment of trimmers

The Raspberry can assign the trimmers to any of the parameters of the ESP32. For example, this can look like this:
```json
{
    "command": "trimmer assignment",
    "assignments": [
        {"vra": "gain_xy", "min": 0.0, "max": 25.0},
        {"vrb": "gain_omega_xy", "min": 0.0, "max": 0.15},
    ]
}
```
The ESP32 will acknowledge the receipt of the command with `{"status": "assigning trimmers"}` and then `{"status": "trimmers assigned"}` (perhaps with additional information on the exact assignment).

#### Completion of initialisation sequence

The initialisation sequence ends when the Pi sends `{"command": "proceed"}` (see above).

Let me hear your thoughts on this.

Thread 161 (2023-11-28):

Acquisition and parsing of GPS data

alphaville, 2023-11-28:
### Describe the solution you'd like

I have uploaded the data we collected on 28/11/23 [https://gist.github.com/alphaville/995a15ef74e8d5b3128c87667b5bfdaf](here). This is how the data looks like

```
$GPGLL,5434.81291,N,00556.15593,W,145737.00,A,A*70
$GPRMC,145738.00,A,5434.81285,N,00556.15627,W,0.351,,281123,,,A*63
$GPVTG,,T,,M,0.351,N,0.650,K,A*27
$GPGGA,145738.00,5434.81285,N,00556.15627,W,1,05,1.28,64.4,M,52.5,M,,*79
$GPGSA,A,3,12,32,24,15,19,,,,,,,,2.51,1.28,2.16*02
$GPGSV,3,1,10,02,02,344,37,12,56,202,22,15,26,166,27,17,,,35*49
$GPGSV,3,2,10,19,34,071,36,22,11,050,32,23,18,236,,24,72,108,35*72
$GPGSV,3,3,10,25,21,223,,32,26,309,41*75
```

### Documentation

The data are structured according to the [NMEA Standard Logs](https://docs.novatel.com/OEM7/Content/Logs/NMEA_Standard_Logs_.htm) protocol. Examples:

1. [GPGLL](https://docs.novatel.com/OEM7/Content/Logs/GPGLL.htm) - Geographic Position
2. [GPGSV](https://docs.novatel.com/OEM7/Content/Logs/GPGSV.htm) - GPS Satellites in View
3. [GPVTG](https://docs.novatel.com/OEM7/Content/Logs/GPVTG.htm) - Track Made Good and Ground Speed

First of all we need to decipher what all these mean and how the data are structured (read the docs).

### Issues to address

1. We interface the GNSS over the serial at a baud rate of `500,000`. We can write a simple interface that reads the data from serial (using `pyserial`) and parses it
2. We should follow what we did [here](https://github.com/QUB-ASL/bzzz/blob/dev/raspberry/bzzz/sensors/anemometer.py) for the anemometer: a thread runs in the background, collects data and stores it in memory, and then we can access is with a non-blocking function (or get a moving average, median, etc).
3. For some reason the data seems to be coming in at 1Hz, which is too slow. Can we speed this up?

alphaville, 2023-11-28:
@pdavid747 @Runway27 Note that if you write your own code you won't have to use `gpsd` at all. Actually you shouldn't use it because it won't let you read the serial. Start by reading the documentation to understand what sort of data we get from the GPS and then build a simple [DTO](https://en.wikipedia.org/wiki/Data_transfer_object): a Python class whose attributes are the quantities the GNSS measures.

alphaville, 2023-12-04:
### Accuracy of GPS measurements and conversion to degrees

⚠️ The GPS coordinates are in degrees-minutes-seconds; after the conversion to a decimal representation, it turns out that the coordinates are fairly accurate.

@pdavid747 use the following function to convert the GPGLL data to degrees:

```python
def deg_min_sec_to_decimal(dms, dir="N"):
    """
    Convert degrees-minutes-seconds from GPGLL to degrees (deciman)

    :param dms: degrees-minutes-seconds (must be positive)
    :param dir: direction (can be one of 'N', 'W', 'E', 'S')
    """
    dms_abs = np.abs(dms)
    degrees = np.floor(dms_abs/100)
    minutes = np.floor(dms_abs - 100 * np.floor(dms_abs/100))
    seconds = 10 * (dms_abs - np.floor(dms_abs))
    deg_decimal_abs = degrees + minutes / 60 + seconds / 3600
    dir_sign = -1 if (dir in ["S", "W"]) else 1
    return dir_sign * deg_decimal_abs
```

alphaville, 2023-12-04:
I installed PyGPSClient on Mac:

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

It allows to set the measurement update rate and many more settings.

alphaville, 2023-12-05:
Scatter plot of estimated positions while static:

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

while being connected to 3-8 satellites (the antenna is placed on metallic plate, but indoors having a decent but not perfect view of the sky; it has an elevation of around 75 degrees). We seem to be getting an accuracy of about ±10m at best, but we might get better results outdoors.

---

Some more results...

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
<p><em>Figure 1.</em> Satellites</p>

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
<p><em>Figure 2.</em> SNR</p>

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
<p><em>Figure 3.</em> Scatter plot (best one)</p>

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
<p><em>Figure 4.</em> Scatter plot</p>

| Parameter              | Value     |
| ------------------ | -------- |
| Satellites in view   | 7 - 9      |
| <span title="Satellites in view">SIV</span> | 7-9 |
| <span title="Satellites in position solution">SIP</span> | 7 |
| <span title="Position dilution of precision">PDOP</span> | 3-3.5 |
| <span title="Horizontal dilution of precision">HDOP</span> | 1.5-3 |

alphaville, 2023-12-05:
### More data

From my other window with 7 satellites (10 in view), pdop: 1.97, and higher SNR

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

jamie-54, 2024-03-07:
Done

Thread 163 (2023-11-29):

Python interface for barometer

alphaville, 2023-11-29:
### Describe the solution you'd like

Some updates may be necessary in [`PressureSensor`](https://github.com/QUB-ASL/bzzz/blob/dev/raspberry/bzzz/sensors/pressure_sensor.py). The barometer can provide useful measurements that along with ToF measurements can improve the estimation of altitude:

### Documentation

All methods - private and public - should be documented. Currently there is no documentation.

### No setters

I suppose setters should not be available:

```python
@altitude.setter
    def altitude(self, val):
        self._current_altitude = val
```

The caller should not be allowed to set a pressure or altitude value.

### Naming conventions

We should update the names of functions and variables to be compatible with PEP8.

### Private methods

Private methods should start with a double underscore (not single)

### Refactoring

It's not clear to me what `_pressure_readings_list` does and why it is (not) initialised with `None` [here](https://github.com/QUB-ASL/bzzz/blob/dev/raspberry/bzzz/sensors/pressure_sensor.py#L36) and then initialised as a list [here](https://github.com/QUB-ASL/bzzz/blob/dev/raspberry/bzzz/sensors/pressure_sensor.py#L53).

In any case, we should probably have an implementation akin to the one for the anemometer.

### Testing

We need to test it again on the new PCB

Yuanbwcx, 2023-12-05:
```@altitude.setter
    def altitude(self, val):
        self._current_altitude = val
```
Although a setter method exists, I think it does not actually perform any substantial setting operations. It raises an exception telling the caller that the property cannot be set directly.

alphaville, 2023-12-05:
@Yuanbwcx exacty - that's what I said in the issue description. I don't think we need a setter.

Yuanbwcx, 2023-12-05:
@alphaville Yes, that make sense.

Yuanbwcx, 2023-12-11:
I suppose '_pressure_readings_list' is to create a list to store pressure data, should we import 'Data Logger' like the one for the anemometer?

alphaville, 2023-12-11:
> I suppose `_pressure_readings_list` is to create a list to store pressure data,

I would ignore the majority of the code that is written there. It is not very well designed.

> should we import `Data Logger` like the one for the anemometer?

Yes, import both `data_logger` and `filters`

Runway27, 2024-02-22:
Can I close this issue as well?

alphaville, 2024-02-23:
@Runway27, yes, I'm closing this now since you merged the corresponding PR.

Closed 2024-02-23.

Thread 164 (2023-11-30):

RFC: Market research for GNSS modules and antennas

alphaville, 2023-11-30:
### Describe the solution you'd like

I'm looking for high-precision GNSS modules. These [ArduSimple simpleRTK2Blite Multiband GNSS Boards](https://www.mouser.co.uk/new/ardusimple/ardusimple-simplertk2blite-boards/) seems to be good candidates. They are priced at around £214 on Mouser.

If we get a couple of modules, my understanding is that we can operate them in a base-rover configuration.

Just before I order this, can we check that (i) it's appropriate for our application, (ii) it's not too large and we're happy with the size, (iii) we've done a proper market research.

alphaville, 2023-11-30:
There's also this [SparkFun breakout](https://www.unmannedtechshop.co.uk/product/sparkfun-gps-rtk-sma-breakout-zed-f9p-qwiic/) with the same module, but seems to be smaller. It's just slightly more expensive (£233)

alphaville, 2023-12-01:
> https://www.mouser.co.uk/ProductDetail/SparkFun/GPS-16481?qs=vmHwEFxEFR8xw%2FiWbXmISw%3D%3D
>
> I think this one would be best value for money as its refresh rate is only 5hz below the more expensive version, as well as that its well documented and we can use it with a usb port.

This uses RTK to give an update rate of 20Hz. We'd have to buy two of these (one for the quadcopter and one for the base station), but this is within our budget.

Which is the more expensive version you're referring to?

pdavid747, 2023-12-01:
[SparkFun GNSS Combo Breakout - ZED-F9P, NEO-D9S](https://robosavvy.co.uk/sparkfun-gnss-combo-breakout-zed-f9p-neo-d9s-qwiic.html)

this one

pdavid747, 2023-12-01:
would we have to buy two of these also?

pdavid747, 2023-12-01:
if not it might be beneficial to go with that one as it will work out cheaper

alphaville, 2023-12-01:
> would we have to buy two of these also?

In the product description they say "With a clear view of the sky, specifically to the South, this combo breakout will deliver centimeter-level accuracy positioning without needing separate RTK or NTRIP corrections!" and "With this board, you will know where your (or any object's) X, Y, and Z location is better than an inch **without needing a separate correction source!**"

I haven't found a comparison between the two modules, though. It would be also good to know whether it works reliable around our corner of the Earth.

Just a thought: if we get two [SparkFun GPS-16481](https://www.mouser.co.uk/ProductDetail/SparkFun/GPS-16481?qs=vmHwEFxEFR8xw%2FiWbXmISw%3D%3D) we have two potential advantages: (i) we can get a NEO module later and connect it to the ZED-F9P, (ii) we'll have redundancy: if one module gets fried, most likely we'll still get decent accuracy and be able to fly (e.g., using SSR corrections).

pdavid747, 2023-12-01:
it illustrates the it is operational around the us and Europe, but its quite vague. I suppose if we found a video of someone using it in the uk we could find out that way

pdavid747, 2023-12-01:
https://www.youtube.com/watch?v=TSkIvtaVZc0

this video is quite useful

alphaville, 2023-12-01:
> https://www.youtube.com/watch?v=TSkIvtaVZc0
>
> this video is quite useful

Good find! Indeed, [Mosaic X5](https://www.unmannedtechshop.co.uk/product/sparkfun-triband-gnss-rtk-breakout-mosaic-x5/) looks great, but it's at £610. However, it provides update rates at 100Hz and sub-cm errors.

alphaville, 2023-12-02:
Some additional information we need to be aware of:

This is what [SparkFun](https://learn.sparkfun.com/tutorials/what-is-gps-rtk) says about RTK:

> [...] an RTK receiver takes in an **RTCM correction stream** and then calculates your location with 1cm accuracy in real time. [...] You’ll also need a source of RTCM correction data. This usually comes from an internet connection or a long distance radio capable of approximately 500 bytes per second. LoRa and LTE-CAT M1 are superb choices for this backhaul.

More precisely we can get RTCM Corrections:

1. From [Skylark](https://www.swiftnav.com/skylark) but there's a monthly subscription of $50
2. By making our own NTRIP server that will provide RTCM corrections ([documentation here](https://learn.sparkfun.com/tutorials/how-to-build-a-diy-gnss-reference-station/all#introduction)); we could actually do that, but we'd need to get a second GNSS module and an antenna, but we can buy a cheaper GNSS module.
3. From the [EUREF Permanent GNSS Network](http://www.epncb.oma.be/_networkdata/data_access/real_time/map.php) and we're lucky that there's a station in Belfast somewhere at the harbour

In anycase, unless we need to fly far away from Belfast (>10km from harbour), we won't need to make our own NTRIP server.

### So, which one do we buy?

[Sparkfun Mosaic X5](https://www.unmannedtechshop.co.uk/product/sparkfun-triband-gnss-rtk-breakout-mosaic-x5/) still seems like a good idea, but without RTCM corrections the accuracy will be poor (around ±1.5m). However, we can get correction data from the Belfast station. The only downside is that an Internet connection is required, but I've already ordered a 4G-enabled WiFi router, so we'll have a connection anywhere we go.

@pdavid747, @jamie-54, @Runway27, @Yuanbwcx, @Minanchi thoughts?

alphaville, 2023-12-02:
**Update:** The Belfast NTRIP station has been down since April 2023 ([link](http://www.epncb.oma.be/_networkdata/siteinfo4onestation.php?station=BFST00GBR)). The closest active RTK is in [Ballymena](http://monitor.use-snip.com/map).

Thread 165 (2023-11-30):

Kill motors when receiver gets disconnected

jamie-54, 2023-11-30:
### Describe the bug

We need to make sure that the motors are killed in case the receiver seems to be disconnected for more than a few milliseconds. We had tested it a few weeks ago, and the motors kept spinning after unplugging the receiver.

### Affected File

_No response_

### Affected Line

_No response_

### To Reproduce

Remove the receiver wires

### Minimum reproducible example

Guys, we should simplify bug reporting!

### Additional context

_No response_

alphaville, 2023-11-30:
We should update `SAFETY.md` with a list of all such safety measures that have been implemented on the quadcopter. We should also be testing that they work after every code update.

alphaville, 2023-12-20:
Regarding simplifying the bug reporting, I'd vote in favour of getting rid of *all* fields. Have a look at [this repo](https://github.com/alphaville/optimization-engine/issues/new/choose) for example.

@jamie-54 @Runway27 Any progress on this issue? I'll be available tomorrow afternoon if you like to chat.

Closed 2024-02-19.

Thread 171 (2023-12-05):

correct paths for data logger and filters

jamie-54, 2023-12-05:
### Describe the bug

Fails to run `python bzzz/raspberry/main.py`

This is due to the path for importing `DataLogger` and `MedianFilter`/`NoFilter` in the `anemometer.py` and `evo_time_of_flight.py` files.

However if I add `bzzz.sensor.` it will run the `main.py` file but then the `anemometer.py` and `evo_time_of_flight.py` files

### Affected File

bzzz/raspberry/bzzz/sensor/anemometer.py

### Affected Line

_No response_

### To Reproduce

_No response_

### Minimum reproducible example

```

```

### Additional context

_No response_

alphaville, 2024-01-18:
I think local imports (when importing a module into another in the same folder) need a dot at the beginning. For example, in [another project] we have the folder `constraints` and there we have the files [`ball1.py`](https://github.com/alphaville/optimization-engine/blob/master/open-codegen/opengen/constraints/ball1.py) and [`simplex.py`](https://github.com/alphaville/optimization-engine/blob/master/open-codegen/opengen/constraints/simplex.py). To import `simplex` into `ball1` [we do](https://github.com/alphaville/optimization-engine/blob/master/open-codegen/opengen/constraints/ball1.py#L2):

```py
from .simplex import Simplex
```

In fact, we use `from ... import ...` to import only the things we need from `simplex.py`.

In [another case](https://github.com/alphaville/optimization-engine/blob/master/open-codegen/opengen/constraints/finite_set.py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), we wanted to import a whole sub-module, so we did:

```py
import opengen.functions as fn
```

Here `opengen` is the name of the top-level model (ours is `bzzz`).

alphaville, 2024-01-18:
@jamie-54 do we have a PR for this?

jamie-54, 2024-01-18:
> @jamie-54 do we have a PR for this?

No, there isn't a branch for this either

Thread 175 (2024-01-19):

RFC: killing and un-killing safety procedure

jamie-54, 2024-01-19:
### Describe the solution you'd like

We're about to merge #172 where to arm the throttle stick needs to be down. Now as we fly, if we panic and kill it and then land, the throttle stick will be not at the zero position. Then, to fly again we'll un-kill it and... boom! At the same time, if while flying, we kill it by mistake we want to be able to un-kill immediately - without start-up routines. Here's an idea: we introduce a timer (~3s) and **once killed for 3s, the throttle stick has to be at zero to un-kill**.

alphaville, 2024-01-22:
@jamie-54 I guess this can be addressed in Python, right? We shouldn't have to change anything in the ESP32 code.

jamie-54, 2024-01-22:
At the minute part of its addressed on the ESP32 if you are free I can show you

Closed 2024-02-05.

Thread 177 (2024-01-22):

Add new 3D printed parts

jamie-54, 2024-01-22:
### Describe the solution you'd like

* [x] Add new controller case files.
* [x] Add new controller case lid files.
* [x] Add GPS base station antenna stand adapter.
* [x] Update edited anemometer case
* [x] Update relevant readme.

Closed 2024-01-30.

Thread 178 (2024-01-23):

Saving data unexpectedly

alphaville, 2024-01-23:
### Describe the solution you'd like

This issue was noticed while working on branch [`feature/110-RC_stick_position_fail_safe`](https://github.com/QUB-ASL/bzzz/blob/feature/110-RC_stick_position_fail_safe/raspberry/main.py).

The message `[LOGGER] saving data` appeared without flipping switch A on the RC followed by an error, which we didn't record. It happened twice I think. The error caused `main.py` to crash.

We need to figure out what's causing this behaviour.

jamie-54, 2024-05-08:
This doesn't seem to be happening any more with refactoring

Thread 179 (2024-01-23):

Refactoring Python code (main.py and more)

alphaville, 2024-01-23:
### Describe the solution you'd like

I think our Python code needs some refactoring. Here are some observations from my side:

### In [`get_radio_data_parse_and_send_to_ESP`](https://github.com/QUB-ASL/bzzz/blob/main/raspberry/bzzz/read_sbus/read_sbus_from_GPIO_receiver.py#L84)

1.we need to get rid of `fake_data` and `force_send_fake_data`
2. In the same function, `return_channel_data` should be removed

### In [`main.py`](https://github.com/QUB-ASL/bzzz/blob/dev/raspberry/main.py)

1. When it comes to printing, we have things like the flag [`enable_printing_cache_to_screen`](https://github.com/QUB-ASL/bzzz/blob/dev/raspberry/main.py#L28C5-L28C36) and [`print_debug`](https://github.com/QUB-ASL/bzzz/blob/dev/raspberry/main.py#L114); instead we should be using a [logger](https://realpython.com/python-logging/)
2. Things like [`rad2deg`](https://github.com/QUB-ASL/bzzz/blob/dev/raspberry/main.py#L120) and [`euler_angles`](https://github.com/QUB-ASL/bzzz/blob/dev/raspberry/main.py#L129) should be moved to a different file; if we need operations with quaternions and/or angles, we should create a class, or a file with functions.
3. It feels that the logging system we have is overly complicated: we log the data in [11 different variables](https://github.com/QUB-ASL/bzzz/blob/05475c9813fbb6334b215aa8dc02d79290ae2090/raspberry/main.py#L52C7-L62C23) and then we pack them in a data frame [in a way](https://github.com/QUB-ASL/bzzz/blob/05475c9813fbb6334b215aa8dc02d79290ae2090/raspberry/main.py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) that is difficult to decipher. We need to see whether we can reuse our [`DataLogger`](https://github.com/QUB-ASL/bzzz/blob/dev/raspberry/bzzz/sensors/data_logger.py).
4. [This part](https://github.com/QUB-ASL/bzzz/blob/05475c9813fbb6334b215aa8dc02d79290ae2090/raspberry/main.py#L298C1-L307C46) where we check the number of consecutive outliers is probably not necessary now because we've implemented filters
5. Lengthy part of code [like this](https://github.com/QUB-ASL/bzzz/blob/05475c9813fbb6334b215aa8dc02d79290ae2090/raspberry/main.py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) should be organised in functions

### See also

- We need to address issues #109 and #118
- As we're going through the Python code, we should consider the issue of configuring ESP from RPi (see #159)

jamie-54, 2024-01-23:
Should we try and fix this issue before #109 #118 and #159 or at the same time?
I've added some documentation to start to address #118 and made a PR #180
If we are going to refactor the python code it might be worth merging what is done so far in PR #180

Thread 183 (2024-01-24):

Tune attitude gains

jamie-54, 2024-01-24:
### Describe the bug

The quadcopter currently is not flying very well, hopefully it is just the gains that need tuned but it seems to be vibrating more than it used to.

### Affected File

_No response_

### Affected Line

_No response_

### To Reproduce

_No response_

### Minimum reproducible example

```

```

### Additional context

_No response_

Closed 2024-01-30.

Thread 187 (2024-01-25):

Documentation to build the drone

jamie-54, 2024-01-25:
### Describe the issue

Add documentation for how to to build the drone from scratch

* [x] Parts list
* [x] how to order PCB's
* [x] Link to 3D printed parts where necessary
* [x] Step by step guide to assemble
* [ ] Video?

### Affected File

_No response_

### Affected Line

_No response_

Closed 2024-05-15.

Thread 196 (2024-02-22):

Initiate threading from main.py

Runway27, 2024-02-22:
### Describe the solution you'd like

We need to initiate threading for the barometer from the main file.

alphaville, 2024-03-01:
@Runway27 Can you take care of this issue? It should be rather straightforward (just import the barometer class and use it)

Runway27, 2024-03-01:
Yes sir. I have already created a branch. And have started working on it. Hopefully it will be completed on Monday.

Runway27, 2024-03-01:
I’m planning to include both barometer and time of flight for the time being. And we can include GPS later.

alphaville, 2024-03-01:
It should be really straightforward. Have a look at [multiple with statements](https://stackoverflow.com/questions/893333/multiple-variables-in-a-with-statement).

Runway27, 2024-03-01:
Yes sir.

jamie-54, 2024-03-02:
> I’m planning to include both barometer and time of flight for the time being. And we can include GPS later.

Include the anemometer as well please, [this](https://github.com/QUB-ASL/bzzz/blob/feature/186-save_wind_data_when_flying/raspberry/main.py) should help

jamie-54, 2024-03-07:
Done

Closed 2024-03-07.

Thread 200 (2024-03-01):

Mount GNSS and Antenna to bzzz

jamie-54, 2024-03-01:
### Describe the solution you'd like

* [x] Mount GNSS Module to lid
* [x] Redesign anemometer case or design a platform to mount the antenna to the carbon fibre tube
* [x] Mount Telemetry radio

I've ordered the [USB cable](https://www.amazon.co.uk/charge-Cable-MYLB-Braided-Charging-Black/dp/B07VCHVH9K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) to connect the GNSS Module to the Pi

jamie-54, 2024-03-01:
I'm going to order [this connector](https://uk.rs-online.com/web/p/coaxial-connectors/4466432), to make it easier to mount the antenna

jamie-54, 2024-03-01:
I was thinking something like this for anemometer case with antenna stand?
What's your thoughts?
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

jamie-54, 2024-03-01:
or maybe like this?

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

alphaville, 2024-03-08:
@jamie-54 will there be some holes through the top plate? How will the antenna be supported?

jamie-54, 2024-03-08:
> @jamie-54 will there be some holes through the top plate? How will the antenna be supported?

Hi, I haven't include holes as they where going to line up along the split in the case and it couldn't really be rotated because of the slot for the cable. I was thinking the double sided tape would be enough to hold it as the antenna is very lightweight?
I have this one printed and on the quadcopter and it looks like it will work well

Closed 2024-03-11.

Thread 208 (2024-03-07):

New Video

jamie-54, 2024-03-07:
### Describe the solution you'd like

Not essential but I think we could add a new video soon of bzzz flying with the anemometer, we will be flying outside very soon so would be good to get some videos of that as well. I also have a video of clips of one of the drones being assembled which could be used as well if we want?

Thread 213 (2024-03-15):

Update Frame support

jamie-54, 2024-03-15:
### Describe the solution you'd like

Add updated frame support

Closed 2024-03-19.

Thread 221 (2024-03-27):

Exiting main loop

jamie-54, 2024-03-27:
### Describe the bug

Data logger causes main loop to exit when it reaches max samples

### Affected File

_No response_

### Affected Line

_No response_

### To Reproduce

_No response_

### Minimum reproducible example

```

```

### Additional context

_No response_

jamie-54, 2024-05-08:
This is the logger in the `main.py` file

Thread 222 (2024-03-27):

Update ESC Calibration documentation

jamie-54, 2024-03-27:
### Describe the issue

* [x] Clear to remove propellers before starting

### Affected File

_No response_

### Affected Line

_No response_

Closed 2024-03-28.

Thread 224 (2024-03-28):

3D Printed parts

jamie-54, 2024-03-28:
### Describe the solution you'd like

 * [x]  Remove old files
 * [x]  Add leg stand for pool noddle
 * [x] Change propeller guard to top and bottom half
 * [x] Update readme

Closed 2024-03-28.

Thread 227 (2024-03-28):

ESC PCB

jamie-54, 2024-03-28:
### Describe the solution you'd like

Create a small PCB to replace the prototype board in the controller case where all the ESCs plug in.
Since this is small we can probably get it printed in Uni.
This is also to make it easier to explain how to build bzzz.

jamie-54, 2024-03-29:
Actually from looking at the [ESCs manual](https://www.hobbywing.com/en/uploads/file/20230321/69381b562c41439ee4451c7152905f10.pdf), Since the small red and black wires are from the BEC and we are now using a UBEC to power everything, should we just directly connect the ESCs signal wire to the ESP PCB via a header? @alphaville @pdavid747 @Yuanbwcx @Runway27 @ejb-11 @Minanchi

Closed 2024-04-12.

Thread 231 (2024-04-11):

Plain controller case lid and base plate .f3d file

jamie-54, 2024-04-11:
### Describe the solution you'd like

* [x] Add the files for a the controller case lid without carbon pole
* [x] Add the .f3d file for the power distribution board support plate

Closed 2024-04-15.

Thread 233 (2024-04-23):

Update GNSS parse to read Relative Position North East Down

jamie-54, 2024-04-23:
### Describe the solution you'd like

Change the GNSS module to read the relative north, east, down postion of the rover GNSS compared to the base station.
[This](https://github.com/mnltake/readF9P_UBX/tree/master) will be useful, if tested it and made a few small changes and was able to print the correct data.

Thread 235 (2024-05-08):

Data Logger Max sample

jamie-54, 2024-05-08:
### Describe the bug

Increasing the size of the max samples causes delays when trying read the most up to date values.
@alphaville This is the underlying issue we had with delays reading the Evo ToF previously when refactoring.

### Affected File

raspberry/bzzz/sensors/data_logger.py

### Affected Line

_No response_

### To Reproduce

Hard code line 67 in the `gnss.py` file and run it.
Increasing the max_samples adds delays when printing the 'current' altitude.

### Minimum reproducible example

```

```

### Additional context

_No response_

jamie-54, 2024-05-09:
This also address the `time.sleep(0.018)` needed in `main.py`

Closed 2024-05-15.

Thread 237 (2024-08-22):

LiDAR Driver

ejb-11, 2024-08-22:
### Describe the solution you'd like

In order to integrate the LiDAR module for use in SLAM, we will need to write a driver to interface with it and read its output. This can partly adapt code from the GNSS module.

ejb-11, 2024-08-22:
When looking up the documentation PDF with the details of the protocol for communicating with the LiDAR, I found this Python library on GitHub that should be suitable: [Robotica/RPLidar](https://github.com/Roboticia/RPLidar). I will test it and provide an update.

ejb-11, 2024-08-22:
Tested using the example programmes (though some had to be modified) and it seems to work well. Doesn't appear to use threading, but perhaps it could be modified to make use of it.

ejb-11, 2024-08-31:
@jamie-54 The driver is mostly finished now, but it still has a number of issues that need to be solved. The background thread takes the lock and never hands it over so that the foreground thread can access its data using a property. I tried to copy the style of your GNSS module. Could you take a look and see what's up? Thanks.

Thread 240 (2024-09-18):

LiDAR Odometry

ejb-11, 2024-09-18:
### Describe the solution you'd like

Odometry is required for SLAM to be performed, which is a challenge since bzzz is a UAV; odometry usually comes from the wheels. There is a technique called "LiDAR map-matching" which can be used to calculate the translation and rotation between scans of the LiDAR, which should be used here.

LiDAR map-matching is not particularly accurate in translation, but is very accurate in rotation. This weakness can be overcome by using the motion data from the IMU as the assumed prior translation for the map-matching, which helps counteract the effects of drift from a purely IMU based odometry setup, and also provides superior sensitivity in translation than in purely LiDAR map-matching based odometry.

By using this approach, the entire need for SLAM can be sidestepped in a way that makes SLAM easier to implement in the future (which is good, since most SLAM approaches available online rely on ROS, or are designed only as prototype benchmarks for algorithms and work offline on complete datasets).

I will present a solution that makes use of the following code:
[https://github.com/1988kramer/intel_dataset/blob/master/scripts/Align2D.py](https://github.com/1988kramer/intel_dataset/blob/master/scripts/Align2D.py)

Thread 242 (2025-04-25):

hardware: tests: tests refer to renamed lib

conquinn99, 2025-04-25:
### Describe the bug

`radio.hpp` and `radio.cpp` were renamed to [raspberryEsp32Interface.hpp](include/raspberryEsp32Interface.hpp) and [raspberryEsp32Interface.cpp](src/raspberryEsp32Interface.cpp) in d730aa5. Multiple tests still refer to `radio.hpp`.

This is currently present in main and dev branches. Probably has been forked onto other branches.

### Affected File

hardware/tests/hw_test_motors.cpp

### Affected Line

4

### To Reproduce

_No response_

### Minimum reproducible example

```

```

### Additional context

_No response_

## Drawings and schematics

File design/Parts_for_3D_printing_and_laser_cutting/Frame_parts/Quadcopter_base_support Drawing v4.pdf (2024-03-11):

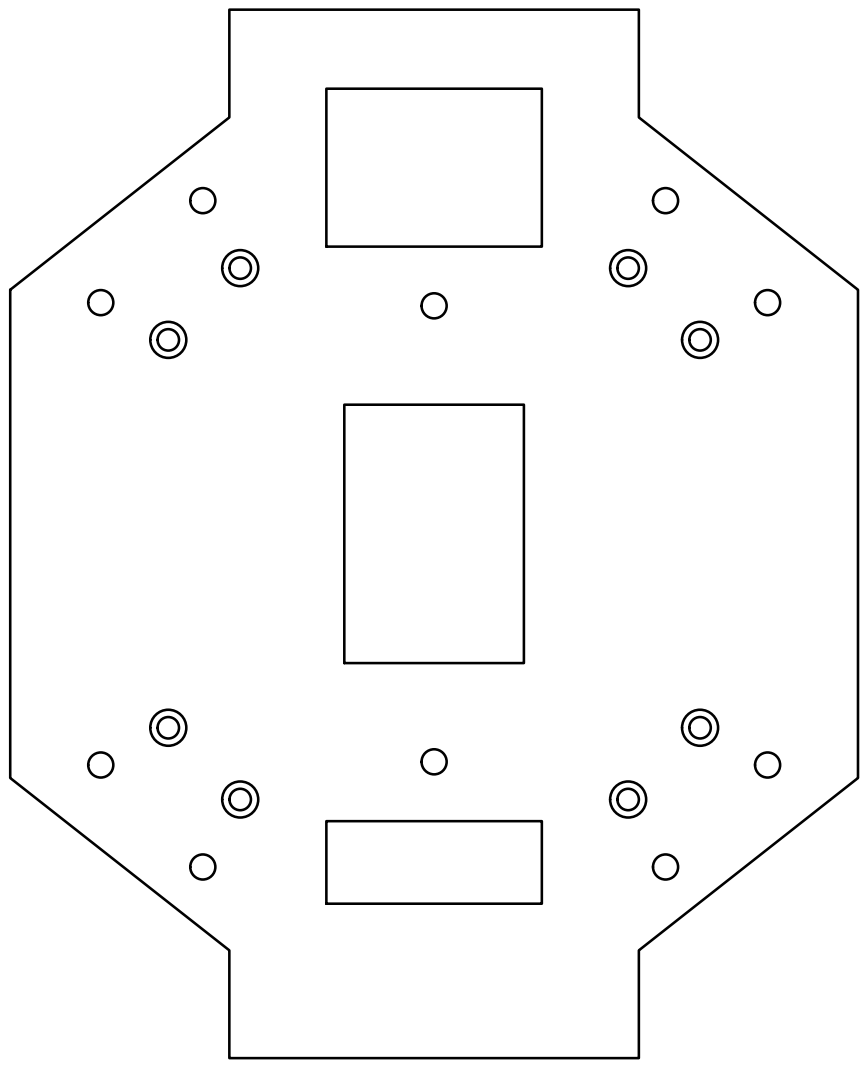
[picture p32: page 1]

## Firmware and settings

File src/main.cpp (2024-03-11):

#include <Arduino.h>
#include "quaternion.hpp"
#include "config.hpp"
#include "motors.hpp"
#include "raspberryEsp32Interface.hpp"
#include "ahrs.hpp"
#include "controller.hpp"
#include "fail_safes.hpp"
#include "util.hpp"

using namespace bzzz;

hw_timer_t *timer = NULL;
portMUX_TYPE timerMux = portMUX_INITIALIZER_UNLOCKED;
MotorDriver motorDriver;
RaspberryEsp32Interface raspberryEsp32Interface(true);
AHRS ahrs;
Controller controller;
Quaternion initialQuaternion;
FailSafes failSafes(TX_CONNECTION_TIMEOUT_IN_uS);
float yawReferenceRad = 0.0;
float initialAngularVelocity[3];
float IMUData[6];
int motorFL, motorFR, motorBL, motorBR;
bool wasKill=0;
bool isKill=0;
unsigned long timestampLastKill = 0;
bool isThrottleStickDown = 0;

/**
 * Here the timer state is declared as a global variable
 * so that it can be accessed by the loop function (and possibly
 * by other interrupts). When accessing `timerState` we should
 * be first acquiring its lock (i.e., the `timerMux`).
 */
volatile bool timerState = true;

/**
 * Callback, attached to the timer interrupt
 * It is generally advisable to keep the implementation of this
 * function as lean as possible (it should just toggle a flag).
 * This function is executed only ONCE every period.
 */
void IRAM_ATTR onTimer()
{
  taskENTER_CRITICAL_ISR(&timerMux);
  timerState = !timerState;
  taskEXIT_CRITICAL_ISR(&timerMux);
}

/**
 * Setup the timer for running the main loop at a fixed rate.
 * timerAlarmWrite is simply a counter; we count a number of
 * timer periods before calling the callback function (onTimer).
 * The second argument is the sampling period in micros.
 */
void setupTimer()
{
  timer = timerBegin(TIMER_ID, TIMER_PRESCALER, true);
  timerAttachInterrupt(timer, &onTimer, true);
  timerAlarmWrite(timer, TIMER_INTERVAL_uS, true);
  timerAlarmEnable(timer);
}

/**
 * Setup the AHRS
 */
void setupAHRS()
{
  ahrs.setup();
  ahrs.preflightCalibrate(false);
  ahrs.calibrateMagnetometer(MAGNETOMETER_BIAS_X, MAGNETOMETER_BIAS_Y, MAGNETOMETER_BIAS_Z,
                             MAGNETOMETER_SCALE_X, MAGNETOMETER_SCALE_Y, MAGNETOMETER_SCALE_Z);
}

/**
 * Setup function
 */
void setup()
{
  setupTimer();                                          // setup the main loop timer
  setupBuzzer();                                         // setup the buzzer
  Serial.begin(SERIAL_BAUD_RATE);                        // start the serial
  setupAHRS();                                           // setup the IMU and AHRS
  ahrs.averageQuaternion(initialQuaternion);             // determine initial attitude
  ahrs.averageAngularVelocities(initialAngularVelocity); // determine initial attitude
  buzz(2);                                               // 2 beeps => AHRS setup complete
  logSerial(LogVerbosityLevel::Info, "waiting for PiSerial...");
  waitForPiSerial(); // wait for the RPi and the RC to connect
  buzz(4);           // 4 beeps => RPi+RC connected
  logSerial(LogVerbosityLevel::Info, "waiting for arm...");
  raspberryEsp32Interface.waitForArmCommand(); // wait for the RC to send an arming command
  logSerial(LogVerbosityLevel::Info, "arming...");
  buzz(2, 400);               // two long beeps => preparation for arming
  motorDriver.attachAndArm(); // attach ESC and arm motors
  buzz(6);                    // 6 beeps => motors armed; keep clear!
}

/**
 * Set controller gain values from RC trimmers
 *
 * Trimmer A - X/Y quaternion gain
 * Trimmer B - X/Y angular velocity gain
 * Trimmer C - Yaw angular velocity gain
 */
void setGainsFromRcTrimmers()
{
  controller.setQuaternionGain(
      -raspberryEsp32Interface.trimmerVRAPercentage() * RADIO_TRIMMER_MAX_QUATERNION_XY_GAIN);
  controller.setAngularVelocityXYGain(
      -raspberryEsp32Interface.trimmerVRBPercentage() * RADIO_TRIMMER_MAX_OMEGA_XY_GAIN);
  controller.setYawAngularVelocityGain(
      -raspberryEsp32Interface.trimmerVRCPercentage() * RADIO_TRIMMER_MAX_OMEGA_Z_GAIN);
}

/**
 * Loop function
 */
void loop()
{  
  taskENTER_CRITICAL_ISR(&timerMux);
  timerState = !timerState;
  taskEXIT_CRITICAL_ISR(&timerMux);

  float quaternionImuData[4];
  float measuredAngularVelocity[3];
  float angularVelocityCorrected[3];

  if (!timerState) return;
  
  // if raspberryEsp32Interface data received update the last data read time.
  if (raspberryEsp32Interface.readPiData())
  {
    raspberryEsp32Interface.sendFlightDataToPi(
        IMUData[0], IMUData[1], IMUData[2], IMUData[3], IMUData[4], IMUData[5],
        motorFL, motorFR, motorBL, motorBR);
    failSafes.setLastRadioReceptionTime(micros());
    
    wasKill = isKill;
    isKill = raspberryEsp32Interface.kill();
    isThrottleStickDown = raspberryEsp32Interface.throttleReferencePercentage() < MAX_ARMING_THROTTLE_PERCENTAGE;
    logSerial(LogVerbosityLevel::Debug, ">> [%d, %d] >> %lu\n",
            isKill, wasKill, timestampLastKill);
  }
  
  // If you're attempting to resurrect it...
  // K --> U
  if (!isKill && wasKill){
    // If you're too late, you need to pull the stick down
    unsigned long timeElapsedSinceKill = millis() - timestampLastKill;
    if (timeElapsedSinceKill >= UN_KILL_KILL_SWITCH_TIMEOUT_IN_ms) {
        if (!isThrottleStickDown){
          motorDriver.disarm();
          isKill = 1;
          return;
        }
    }
  } 

  // one function to run all fail safe checks
  if (isKill || failSafes.isSerialTimeout())
  {
    if (!wasKill) {
      // U --> K
      timestampLastKill = millis();
    }
    motorDriver.disarm();
    return; // exit the loop
  }

  ahrs.update();
  setGainsFromRcTrimmers();
  ahrs.quaternion(quaternionImuData);
  ahrs.angularVelocity(measuredAngularVelocity);

  // Determine correct angularVelocity
  angularVelocityCorrected[0] = measuredAngularVelocity[0] - initialAngularVelocity[0];
  angularVelocityCorrected[1] = measuredAngularVelocity[1] - initialAngularVelocity[1];
  angularVelocityCorrected[2] = measuredAngularVelocity[2] - initialAngularVelocity[2];

  float yawRateRC = raspberryEsp32Interface.yawRateReferenceRadSec();
  float deadZoneYawRate = 0.017;
  float yawRateReference = 0.;
  if (yawRateRC >= deadZoneYawRate)
  {
    yawRateReference = yawRateRC - deadZoneYawRate;
  }
  else if (yawRateRC <= -deadZoneYawRate)
  {
    yawRateReference = yawRateRC + deadZoneYawRate;
  }

  // take the current Yaw angle as reference, this means that we are not correcting the Yaw.
  yawReferenceRad = ahrs.currentYawRad();

  Quaternion referenceQuaternion(
      yawReferenceRad,
      raspberryEsp32Interface.pitchReferenceAngleRad(),
      raspberryEsp32Interface.rollReferenceAngleRad());

  Quaternion currentQuaternion(quaternionImuData);
  Quaternion relativeQuaternion = currentQuaternion - initialQuaternion;
  Quaternion attitudeError = referenceQuaternion - relativeQuaternion; // e = set point - measured

  IMUData[0] = relativeQuaternion[1];
  IMUData[1] = relativeQuaternion[2];
  IMUData[2] = relativeQuaternion[3];
  ahrs.getAccelerometerValues(IMUData + 3);

  // Throttle from RC to throttle reference
  float throttleRef = raspberryEsp32Interface.throttleReferencePWM();

  // Compute control actions and send them to the motors

  controller.motorPwmSignals(attitudeError,
                            angularVelocityCorrected,
                            yawRateReference,
                            throttleRef,
                            motorFL, motorFR, motorBL, motorBR);
  
  motorDriver.writeSpeedToEsc(motorFL, motorFR, motorBL, motorBR);


  logSerial(LogVerbosityLevel::Debug, "PR: %f %f\n",
            IMUData[1], IMUData[2]);
}

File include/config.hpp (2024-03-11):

#include <Arduino.h>

#ifndef GLOBALS_H
#define GLOBALS_H

/**
 * Timer config
 */
#define TIMER_ID 0
#define TIMER_PRESCALER 80
#define TIMER_INTERVAL_uS 4000

// Various defines such as PIN numbers and global constants

/**
 * IMU config
 */
#define IMU_ADDRESS (0x68)

/**
 * Serial config
 */
#define SERIAL_BAUD_RATE 500000

/** Sampling time */
#define SAMPLING_TIME (0.008)

/*
 * AHRS config
 */
#define MAGNETOMETER_BIAS_X -251.054
#define MAGNETOMETER_BIAS_Y -43.154
#define MAGNETOMETER_BIAS_Z -226.343

#define MAGNETOMETER_SCALE_X 1.013
#define MAGNETOMETER_SCALE_Y 0.981
#define MAGNETOMETER_SCALE_Z 1.006

/*
 * Motors config
 */
#define FRONT_LEFT_ESC_PIN 25
#define FRONT_RIGHT_ESC_PIN 33
#define BACK_LEFT_ESC_PIN 27
#define BACK_RIGHT_ESC_PIN 26

#define ARM_ROTOR_SPEED 900
#define ZERO_ROTOR_SPEED 1000
#define IDLE_ROTOR_SPEED 1130
#define ABSOLUTE_MIN_PWM 800
#define ABSOLUTE_MAX_PWM 2000

/**
 * Buzzer pin
 */
#define BUZZER_PIN 32

/**
 * Maximum throttle percentage for arming the motors
 * The throttle stick must be less than this percentage to arm the motors
 */
#define MAX_ARMING_THROTTLE_PERCENTAGE 0.05

/** Maximum pitch value corresponding to the top position of the stick (30deg = 0.52rad) */
#define PITCH_MAX_RAD 0.5235987755982988

/** Value from the radio when the stick is at the lowest position */
#define RADIO_STICK_MIN 300

/** Value from the radio when the stick is at the highest position */
#define RADIO_STICK_MAX 1700

/** Maximum yaw rate (rad/s) 10 deg/s = 0.1745 rad/s */
#define RADIO_MAX_YAW_RATE_RAD_SEC 0.1745

/** Trimmer A on RC - maximum quaternion XY gain */
#define RADIO_TRIMMER_MAX_QUATERNION_XY_GAIN 100.
/** Tested attitude Quaternion roll-pitch axis control gain*/
#define QUATERNION_XY_GAIN 0.470

/** Trimmer B on RC - maximum quaternion Z gain */
#define RADIO_TRIMMER_MAX_QUATERNION_Z_GAIN 100.

/** Trimmer C on RC - maximum omega xy gain */
#define RADIO_TRIMMER_MAX_OMEGA_XY_GAIN 0.3
/** Tested attitude angular velocity roll-pitch axis control gain*/
#define OMEGA_XY_GAIN 0.305

/** Trimmer E on RC - maximum omega z gain */
#define RADIO_TRIMMER_MAX_OMEGA_Z_GAIN 4
/** Tested attitude angular velocity yaw axis control gain*/
#define OMEGA_Z_GAIN 0.111

/**
 * Control action to PWM scaling factor
 */
#define U_TO_PWM 8

/**
 * Fail-safe config
*/
#define TX_CONNECTION_TIMEOUT_IN_uS 500000
#define UN_KILL_KILL_SWITCH_TIMEOUT_IN_ms 3000

#ifndef BZZZ_LOGGING_LEVEL
#define BZZZ_LOGGING_LEVEL 3
#endif

#endif /* GLOBALS_H */

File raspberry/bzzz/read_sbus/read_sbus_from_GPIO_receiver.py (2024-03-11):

import bzzz.read_sbus.read_sbus_from_GPIO
import time
import serial
import bzzz.read_sbus.radioDataParser
import threading
from bzzz.sensors.evo_time_of_flight import EvoSensor

class RC:
    """
    This class is used to interface the remote control (receiver) with the Raspberry Pi.
    """

    def __init__(self,
                 serial_path='/dev/ttyUSB0',
                 baud=500000,
                 sbus_pin = 25):
        """
        Create a new instance of RC

        :param serial_path: serial path; defaults to /dev/ttyUSB0 on RPi
        :param baud: baud rate of serial communication; defaults to 500000
        :param sbus_pin: RPi GPIO pin where RC receiver sbus wire is plugged in
        """
        # Time of flight sensor
        self.__ToF_seansor = EvoSensor()

        # serial connection between Pi and ESP32
        self.ser = serial.Serial(serial_path, baud, timeout=1)
        self.ser.reset_input_buffer()
        self.reader = bzzz.read_sbus.read_sbus_from_GPIO.SbusReader(sbus_pin)
        self.reader.begin_listen()

        # wait until connection is established
        still_waiting = False
        while (not self.reader.is_connected()):
            print("{still_waiting_text}aiting for radio connection to establish....".format(
                still_waiting_text="Still w" if still_waiting else "W"))
            time.sleep(.2)
            still_waiting = True

        # Note that there will be nonsense data for the first 10ms or so of connection
        # until the first packet comes in.
        time.sleep(.1)
        self.parser = bzzz.read_sbus.radioDataParser.RadioDataParser()

        self.__parsed_data = None

    def get_radio_data(self,
                       max_packet_age_in_ms=500,
                       receiver_disconnect_throttle_ref=650,
                       receiver_disconnect_throttle_height = 0.6):
        """
        Checks if the radio is connected, determines when the last RC data was received
        and reads the 16 channels of data received from the RC

        :param max_packet_age_in_ms: max age a packet can be im ms. Therefore how long the quadcopter
                                     can fly since it last read the receiver. defualt 500ms
        :parm receiver_disconnect_throttle_ref: Throttle refrence that can be set, that if the receiver disconnects
                                                the throttle will be set to this value which should be slightly less 
                                                than the hovering throttle. defualt 650 ROUGH ESTIMATION
        :parm receiver_disconnect_throttle_height: How close the quadcopter has to be to the ground to kill the motors
                                                   if the receiver disconects. Above this hieght the motor will spin 
                                                   at a speed according to the 'receiver_disconnect_throttle_ref' param
                                                   defualt 0.6m

        Returns:
        If the receiver is connected
        When the last RC data was received
        16 channels of data received from RC
        """
        is_connected = self.reader.is_connected()
        packet_age = self.reader.get_latest_packet_age()  # milliseconds

        # returns list of length 16, so -1 from channel num to get index
        if packet_age > max_packet_age_in_ms or not is_connected:
            if self.__ToF_seansor.distance > receiver_disconnect_throttle_height:
                channel_data = str(f"1000, 1000, {receiver_disconnect_throttle_ref}, 1000, 300, {self.reader.translate_latest_packet()[5]}, \
                                   {self.reader.translate_latest_packet()[6]}, {self.reader.translate_latest_packet()[7]}, 1700, 300, 300, 1700, 1000, 1000, 1000, 1000")
            else:
                channel_data = str(f"1000, 1000, 300, 1000, 300, {self.reader.translate_latest_packet()[5]}, {self.reader.translate_latest_packet()[6]}, \
                                   {self.reader.translate_latest_packet()[7]}, 1700, 300, 1700, 1700, 1000, 1000, 1000, 1000")
        else:
            channel_data = str(self.reader.translate_latest_packet())[1:-1]

        return is_connected, packet_age, channel_data

    def parse_radio_data(self, 
                         channel_data,
                         over_write_throttle_ref_to=-1):
        """
        This function checks that the channel data from the remote is in the correct range and then formates it correctly to be sent to the ESP32.
        
        :param channel_data: The channel data from the remote that we want to check is in the correct range
        :param over_write_throttle_ref_to: When altitude hold is active we want to overwrite the throttle reference from the remote. 
               This sends the new throttle value, if set to -1 the reference throttle is kept; default: -1.
        """
        # check if data is in range [1000, 2000]
        self.parser.m_channelData = list(map(lambda x: 0 if int(x) < 0 else (
            2000 if int(x) > 2000 else int(x)), channel_data.strip().split(",")))

        if over_write_throttle_ref_to != -1:
            # TODO: check if channel 2 is throttle data
            self.parser.m_channelData[2] = over_write_throttle_ref_to
        # process and encapsulate the data
        # the output data packet format will be as follows
        # Y_radPs, P_rad, R_rad, T_PWM_MIN2MAX, % trimA, % trimB, % trimC, % trimE, encodedSwitchesData
        # here the final data value encodedSwitchesData is an integer carrying information
        # of the position of switches A, B, C, and D in the last 5-bits (the rightmost 5-bits),
        # in which each bit corresponds to data as follows
        # bit-4 (MSB): 1-bit info of Switch B: 1 if armed else 0
        # bit-3: 1-bit info of Switch A: 1 if kill_on else 0
        # bits 2 and 1: 2-bit info of switch C: 00 for position DOWN, 01 for position MID, 10 for position UP
        # bit-0: 1-bit info of switch D: 1 if D_on else 0
        self.__parsed_data, channel_data = self.parser.format_radio_data_for_sending()
        return channel_data

    def send_data_to_ESP(self, channel_data):
        # Send with S in the beginning to indicate the start of the data, and also useful to check if data
        # is received properly on the ESP's end
        # Send data from Pi to ESP32, send a new line char so ESP32 knows when to stop reading
        self.ser.write(f'S,{channel_data}\n'.encode())

    def receive_data_from_ESP(self):
        """
        Read data from ESP32 via UART.

        :return: String if data is received, None otherwise.
        """
        while self.ser.inWaiting() > 0:
            try:
                line = self.ser.readline().decode('ascii').rstrip()
                return line
            except UnicodeDecodeError as e:
                print(f"UnicodeDecodeError {e}, retrying....")
        else:
            return None
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

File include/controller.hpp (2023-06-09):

#include "config.hpp"
#include "quaternion.hpp"

#ifndef CONTROLLER_H
#define CONTROLLER_H

namespace bzzz
{

    class Controller
    {
    private:
        /**
         * Gain values for the quaternion
         */
        float m_quaternionGain[3] = {-17., -17., -0.98};

        /**
         * Gain values for the angular velocity
         */
        float m_angularVelocityGain[3] = {-1.4, -1.55, -1.08};

        /**
         * @brief computes control action
         *
         * @param attitudeError attitude error quaternion
         * @param angularVelocity angular velocity (from IMU)
         * @param control control actions (3-array)
         *
         */
        void controlAction(
            Quaternion &attitudeError,
            const float *angularVelocity,
            float angularVelocityYawRef,
            float *control);

    public:
        /**
         * Constructs a new instance of Controller
         */
        Controller();

/*
The following functions should only be defined/used when in debug mode.
The idea is to allow to fine-tune the gain values using the trimmers on
the RC.
*/
#ifdef BZZZ_DEBUG
        /**
         * Set the gains of the quaternion
         */
        void setQuaternionGain(float gainXY);

        /**
         * Set the gains of omega_x and omega_y
         */
        void setAngularVelocityXYGain(float gainOmegaXY);

        /**
         * Set the gains of the angular velocity
         */
        void setYawAngularVelocityGain(float gainOmegaZ);
#endif /* BZZZ_DEBUG */

                /**
         * @brief PWM signals to the four motors
         *
         * @param attitudeError attitude error quaternion
         * @param angularVelocity angular velocity (from IMU)
         * @param angularVelocityYawRef angular velocity (yaw) reference
         * @param throttle throttle signal (between 1000 and 2000)
         * @param motorFL signal to front left motor
         * @param motorFR signal to front right motor
         * @param motorBL  signal to back left motor
         * @param motorBR signal to back right motor
         * @param controlToPwmScaling (optional) scaling parameter
         * @param motorClipLow (optional) lowest value of motor signal [default: 1000]
         * @param motorClipHigh highest value of motor signal [default: 2000]
         */
        void motorPwmSignals(
            Quaternion &attitudeError,
            const float *angularVelocity,
            float angularVelocityYawRef,
            float throttle,
            int &motorFL,
            int &motorFR,
            int &motorBL,
            int &motorBR,
            float controlToPwmScaling = U_TO_PWM,
            int motorClipLow = ZERO_ROTOR_SPEED,
            int motorClipHigh = ABSOLUTE_MAX_PWM);

    }; /* end of class Controller */

} /* end of namespace bzzz */

#endif /* CONTROLLER_H */

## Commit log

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2023-04-09 Use new IMU interface in main.cpp and set baud rate to 115200 in platformio.ini
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2023-04-12 Updated Motor related files. main.cpp updated to test the motor. config.hpp updated for correct ESC pins. gitignore updated
    [config.hpp, main.cpp, motors.cpp]
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2023-04-19 Add TorqueSystem (motor) class, fixed radio issues
    [config.hpp, hw_test_motors.cpp, main.cpp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]
2023-04-19 integration of individual components
    new quaternion class implementation
    first version of controller
    getter for angular velocity in AHRS
    main.cpp: experimental integration
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2023-04-21 fix typo in initial attitude
    [main.cpp]
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2023-05-01 Reverted back to commit 65a4af3 and resolved issues. changed motors.cpp file, no need for ESC library. updated ahrs.cpp file to read correct quaternion. updated ESC pins in config.hpp.
    [config.hpp, main.cpp, motors.cpp]
2023-05-02 fixed issue 24, updated initial quaternion
    [main.cpp]
2023-05-04 updated hw_test_ahrs to show quaternion and angular velocities updated euler angles to use quaternion function
2023-05-06 Implementation of fail-safes
    check arming switch in setup
    check kill switch in loop
    disarm and exit loop if killed
    [main.cpp]
2023-05-08 Waiting for arm signal from RC
    About:
    Change (again) readPiData to return bool
    Remove readRadioData
    Implement setupBuzzer and buzz in main
    Define BUZZER_PIN in config.hpp
    Issues:
    Addresses #29
    [config.hpp, main.cpp]
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2023-05-10 wait for pi to send data
    create function in main
    waiting for RPi to send data over serial
    remove RC_ESC as a dependency from platformio.ini
    May partially address #28
    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
    [main.cpp]
2023-05-10 Moved buzz from setupMotor to main setup to match rest of Buzz
    [main.cpp]
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2023-05-10 Tidy up main.cpp
    - average initial attitude computed in ahrs (averageQuaternion)
    - new method in motor driver
    - new method in radio
    - Addresses #41
    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
    [main.cpp, motors.cpp]
2023-05-10 Utilities moved to util
    - logSerial, setupBuzzer, buzz and waitForPiSerial go to util
    - delete config.cpp
    - change Serial.print to logSerial
    - deactivate printing while flying
    - rename BZZZ_VERBOSITY to BZZZ_LOGGING_LEVEL
    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
    [config.hpp, main.cpp, util.cpp]
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2023-05-26 added fail-safe support for transmitter connection timeout
    [main.cpp, read_sbus_from_GPIO_receiver.py]
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2023-05-29 fixed type conversion mistakes
    [radioDataParser.py, read_sbus_from_GPIO_receiver.py]
2023-05-29 added serial print in main.cpp to check if data is being received correctly
    [main.cpp, read_sbus_from_GPIO_receiver.py]
2023-05-29 fixed logical errors, now R-Pi processes data properly before sending and ESP is properly decoding the data.
    [main.cpp, radioDataParser.py, read_sbus_from_GPIO_receiver.py]
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2023-05-29 multi-threading in R-Pi, fixed some logical errors in radio.cpp, and main.cpp, increased baud to 500000 from 115200. Everything is working stably. The ESC weird behaviour is fixed. Data is being proc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
    [config.hpp, main.cpp, read_sbus_from_GPIO_receiver.py]
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2023-06-01 removed TODO in read_sbus_from_GPIO_receiver.py and made it in to issue #58.
    [read_sbus_from_GPIO_receiver.py]
2023-06-01 Fixed incompatibility between ThreeWaySwitch and bit shift operator.
    [radioDataParser.py, read_sbus_from_GPIO_receiver.py]
2023-06-02 Fixed logical error in readPiData function.
    [read_sbus_from_GPIO_receiver.py]
2023-06-03 added shematics and PCB design files V0.1, needs review.
    [Drill_NPTH_Through.DRL, Drill_PTH_Through.DRL, Drill_PTH_Through_Via.DRL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]
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2023-06-06 Fail-safe code for halting the drone when Tx connection is lost for 500ms. Code tested.
    [config.hpp, main.cpp, read_sbus_from_GPIO_receiver.py]
2023-06-06 API changed of FailSafes
    - FailSafes() is made private
    - FailSafes constructor takes a motor driver ptr
    - motorDriver -> m_motorDriver
    - remove setMotorDriverObjPtr
    - automatic code formatting
    - update main.cpp accordingly
    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
    [config.hpp, main.cpp]
2023-06-06 Make sure FailSafes is initialised properly
    - motorDriver becomes a reference
    - so it cannot be NULL
    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
    [main.cpp]
2023-06-06 Reverting commit + simplification
    - Make API more SOLID
    - FailSafe now independent of MotorDriver
    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
    [config.hpp, main.cpp]
2023-06-06 made changes suggested in review 1.
    [Drill_NPTH_Through.DRL, Drill_PTH_Through.DRL, Drill_PTH_Through_Via.DRL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]
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2023-06-07 Changes: in introduced yaw-control, in changed kill to swC (states 1 and 2 are kill), in increased gain maxs, in corrected yaw rate reference formula.
    [config.hpp, main.cpp, radioDataParser.py]
2023-06-07 Added basic yaw rate controller code. Changes: in main.cpp made yawRef=currentYaw and command yaw rate instead, in hrs introduced a function to get the current yaw from quaternions.
2023-06-08 yaw rate controller implementation
    - yaw controller based on w_z only
    - change trimmers (ABC only)
    - remove q_z from controller
    - API changes in controller.hpp
    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
2023-06-08 Changes: in `radio.cpp` changed the kill switch to `switchD`, in `controller.cpp` changed `control[2] += m_angularVelocityGain[2] * yawRateError;` to `control[2] = m_angularVelocityGain[2] * yawRateE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
2023-06-08 Changed the ESC headers position on the ESP board PCB to the place where Jamie suggested.
2023-06-09 Adjusted positions of PORT_3 and PORT_4, updated the Gerber files accordingly.
    [Drill_NPTH_Through.DRL, Drill_PTH_Through.DRL, Drill_PTH_Through_Via.DRL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]
2023-06-09 Added current limiting resistor to the Buzzer.
    [Drill_NPTH_Through.DRL, Drill_PTH_Through.DRL, Drill_PTH_Through_Via.DRL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]
2023-06-13 Added mounting holes, and made sure that the mounting holes match those on R-Pi 4B.
    [Drill_NPTH_Through.DRL, Drill_PTH_Through.DRL, Drill_PTH_Through_Via.DRL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]
2023-06-14 Implemented a Kalman filter for altitude and its related paramaters estimation. The file includes a small test simulation as well.
2023-06-14 fixed mismatch between simulation sampling frequency and Kalman filter sampling frequency. Now both are set to 10Hz.
2023-06-18 R-Pi shield and sensor board shcematics and PCBs.
    [Drill_NPTH_Through.DRL, Drill_PTH_Through.DRL, Drill_PTH_Through_Via.DRL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]
2023-06-18 minor PCB layout changes.
    [Drill_NPTH_Through.DRL, Drill_PTH_Through.DRL, Gerber_BoardOutlineLayer.GKO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]
2023-06-19 Added mounting holes for Sensor board.
    [Drill_NPTH_Through.DRL, Drill_PTH_Through.DRL, Drill_PTH_Through_Via.DRL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]
2023-07-03 Version 2 of sensor board, fusion schematic, board layout and gerber files included.
    [copper_bottom.gbr, copper_top.gbr, drill_1_16.xln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]
2023-07-04 Updated the drill files in the manufacturing files folder to reflect changes
    [copper_bottom.gbr, copper_top.gbr, drill_1_16.xln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]
2023-07-05 Removed old Sensor board designs
    [Drill_NPTH_Through.DRL, Drill_PTH_Through.DRL, Drill_PTH_Through_Via.DRL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]
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2023-07-28 Added new schematics with updated mounting holes
    [copper_bottom.gbr, copper_top.gbr, drill_1_16.xln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]
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2023-08-04 Fixed SCL trace on sensor board
    [copper_bottom.gbr, copper_top.gbr, drill_1_16.xln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]
2023-08-04 Fixed SCL trace on sensor board and png image
    [copper_bottom.gbr, copper_top.gbr, drill_1_16.xln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]
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2023-08-17 fixed small typo in main.cpp
    [main.cpp]
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2023-08-17 altitude hold controller
    - complete implementation of altitude hold controller
    - tested on quadcopter
    - credit to @gunturiCM
    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
    [testdata.csv, testdata_2.csv, total_flight_data.csv]
2023-08-17 (re)moved files
    [testdata.csv, testdata_2.csv, total_flight_data.csv]
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2023-08-21 readme file for data
    [testdata.csv, testdata_2.csv]
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2023-08-21 read_sbus_from_GPIO_receiver: still waiting (quick fix)
    [read_sbus_from_GPIO_receiver.py]
2023-08-21 bug fixes and more
    safety check: are switches initially at the correct position
    bug fix in altitude_LQR
    saving logs in separate folder (logs)
    include header in CSV
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2023-08-21 Revert "Added RC switches and throttle check before drone starts."
    This reverts commit 6692c55d14dde0e04b38b7e35d87198419349587.
    [hw_test_receiver.py]
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2023-08-25 Added current .stl files of parts that have been 3D printed and .dxf files of parts for laser cutting
    [Mirrored Threaded top stand with hole set with offset hole. v4.STL, Mirrored rotor guard rev 4.STL, Quadrotor_controller_case v5.stl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]
2023-09-12 fixed mag bais to same as main branch
    [config.hpp]
2023-09-13 Added U,V,W axis and upload first recorded data
    [12-09-23--22:02.csv, 12-09-23--22:37.csv]
2023-09-26 recorded wind data
    [16-09-23--18:35.csv, 16-09-23--18:50.csv, 25-09-23--16:49.csv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]
2023-09-26 update header files
    [16-09-23--18:35.csv, 16-09-23--18:50.csv, 25-09-23--16:49.csv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]
2023-09-26 renaming files to work with git
    [12-09-23--22-02.csv, 12-09-23--22-37.csv, 16-09-23--18-35.csv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]
2023-10-05 Added all fusion360 and stl files for 3D printed parts
    [Amemometer_case v2.f3d, Amemometer_case v2.stl, Mirrored Threaded top stand with hole set with offset hole. v4.STL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]
2023-10-06 Added non rotating motor stands
    [non_rotating_motor_stand v11.f3d, non_rotating_motor_stand v11.stl, non_rotating_motor_stand_set v1.f3d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]
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2023-10-10 updated PCBs
    [Drill_NPTH_Through.DRL, Drill_PTH_Through.DRL, Drill_PTH_Through_Via.DRL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]
2023-10-26 updated platformio file as new servo library cuases issues
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2023-10-27 updating Motor stands, larger center hole
    [non_rotating_motor_stand v11.f3d, non_rotating_motor_stand v11.stl, non_rotating_motor_stand v12.f3d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]
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2023-11-21 anemometer: fix typo in api docs
    [anemometer.py]
2023-11-22 folder restructuring and we got rid of old anemometer files
    [12-09-23--22-02.csv, 12-09-23--22-37.csv, 16-09-23--18-35.csv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]
2023-11-23 Fixed error when no log file
    [anemometer.py]
2023-11-23 corrected timestamp to be recorded
    [anemometer.py]
2023-11-23 fixed filters
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2023-11-30 filters.py: fix typo
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2023-12-06 Will not arm unless switches are correct and throttle less than 5%
    [raspberryEsp32Interface.cpp]
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2023-12-12 Fixes the issue of the motors not working if the kill has been activated previously and the throttle is above 5%
    [main.cpp]
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2024-01-22 update config.hpp ESC and buzzer pins to match new PCB's
    [config.hpp]
2024-01-22 Extra safety measure
    - Addressing issue Â#175
    - Tested on bzzz; seems to be working ok
    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
    [main.cpp]
2024-01-22 Adding new 3D printed parts
    [Amemometer_case v2.f3d, Amemometer_case v2.stl, Amemometer_case v5.f3d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]
2024-01-24 update base station
    [Base_station_adapter v3.f3d, Base_station_adapter v3.stl, Base_station_adapter v7.f3d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]
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2024-02-05 implementation of fixed rate timer for main lopp in main.cpp
    [config.hpp, main.cpp]
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2024-03-04 this code works, added nan values if nothing can be read to prevent errors. those nan vaues are then skipped over in the output
    [gnss.py]
2024-03-07 Replace TOF sensor
2024-03-07 uploaded new anemometer case with gnss antenna stand, added quadcopter base support for laser cutting
    [Amemometer_case v5.f3d, Amemometer_case v5.stl, Amemometer_case v6.f3d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]
